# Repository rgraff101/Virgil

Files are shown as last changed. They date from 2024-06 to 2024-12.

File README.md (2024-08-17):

# BearCart

BearCart is an autonomous driving project. The goal is to upgrade an off-the-shelf
RC car into an AI powered self-driving platform. The software is running on a
Raspberry Pi 5 SBC in its native operating system: Raspberry Pi OS.
Visit [documentations](https://ucaengineeringphysics.github.io/BearCart/) for more details.
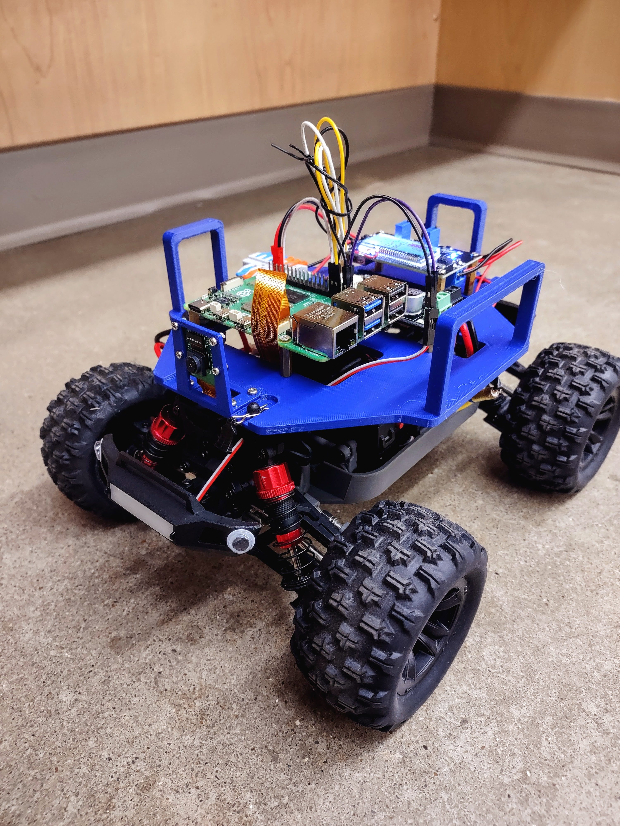
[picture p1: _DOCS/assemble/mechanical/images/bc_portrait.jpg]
portrait


This project is strongly inspired by the 
[DonkeyCar](https://github.com/autorope/donkeycar) project.

## Quick Start
Fire up the terminal on your Raspberry Pi, and run following commands in it.

### Install Dependencies 
```bash
sudo apt install python3-pip
pip install pip --upgrade --break-system-packages
```

### Clone The Repository
```bash
cd ~
git clone https://github.com/UCAEngineeringPhysics/BearCart.git
```

### Install Python Packages
```bash
cd ~/BearCart
pip install -r requirements.txt --break-system-packages
```

## Demo Videos
- [Initial BearCart](https://youtube.com/shorts/Kcm6qQqev3s)
- [Another Autopilot](https://youtu.be/8GX6HnfgrJQ)

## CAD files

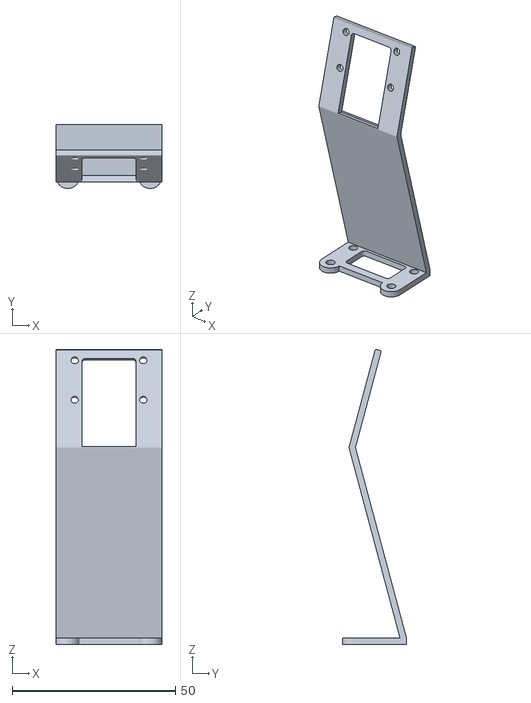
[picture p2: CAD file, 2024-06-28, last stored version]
_DOCS/mechanical_specs/3dprint/CameraMountTall.stl
32.4 x 19.6 x 90.3

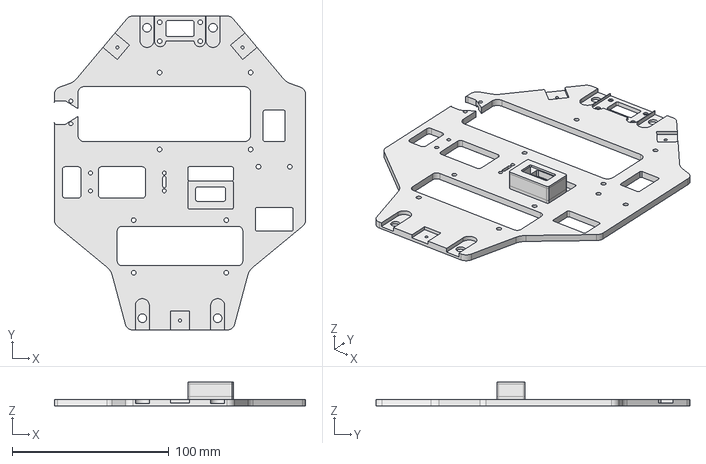
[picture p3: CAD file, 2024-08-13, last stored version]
mechanical_designs/mew4_bed_v3.FCStd
160.0 x 200.0 x 15.2 mm

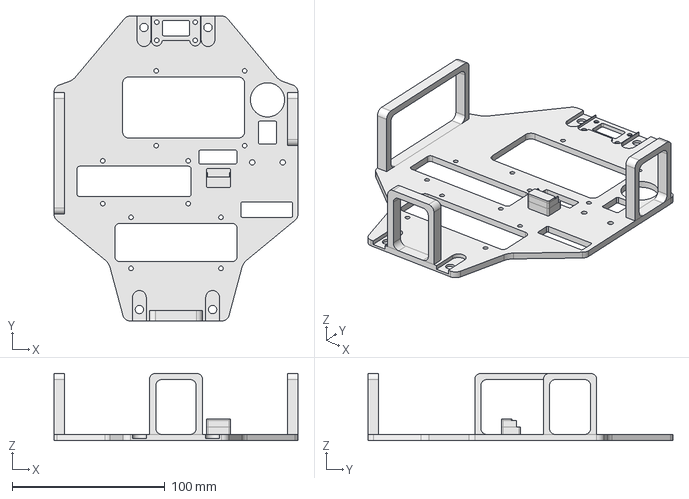
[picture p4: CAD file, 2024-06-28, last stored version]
_DOCS/mechanical_specs/3dprint/mew4_bed_v2.FCStd
160.0 x 200.0 x 44.0 mm

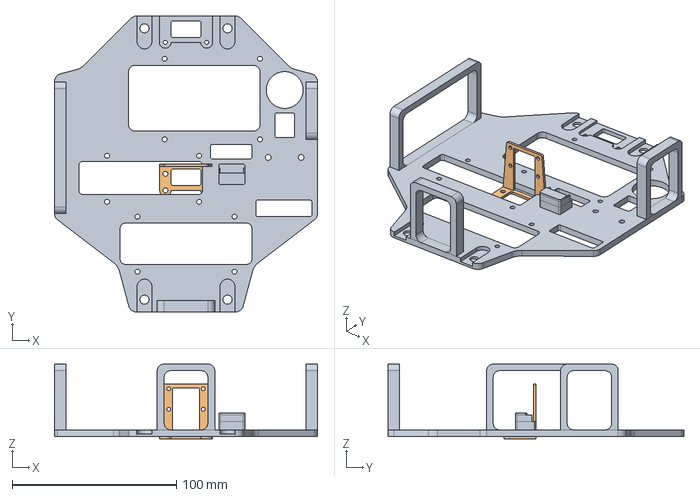
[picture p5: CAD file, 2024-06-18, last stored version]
_DOCS/mechanical_specs/3dprint/haiboxing_bed.FCStd
160.0 x 180.0 x 45.5 mm
CameraMount

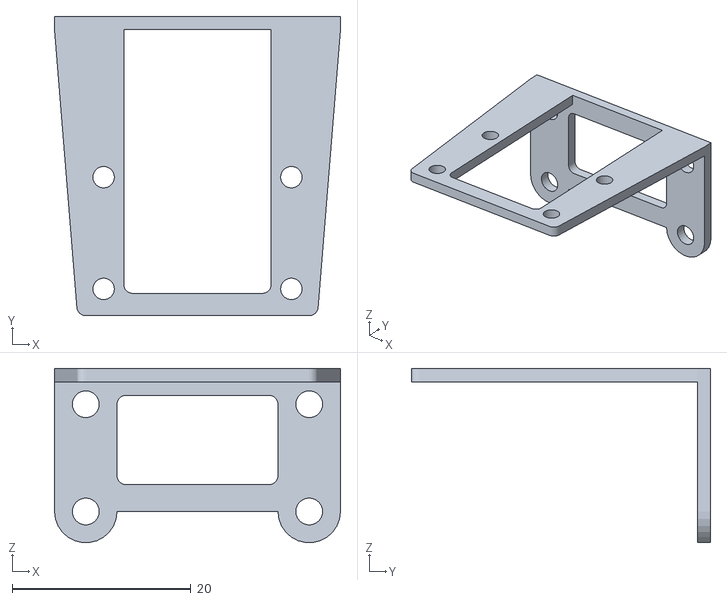
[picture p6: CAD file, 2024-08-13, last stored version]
mechanical_designs/CameraMount.stl
32.0 x 33.5 x 19.5

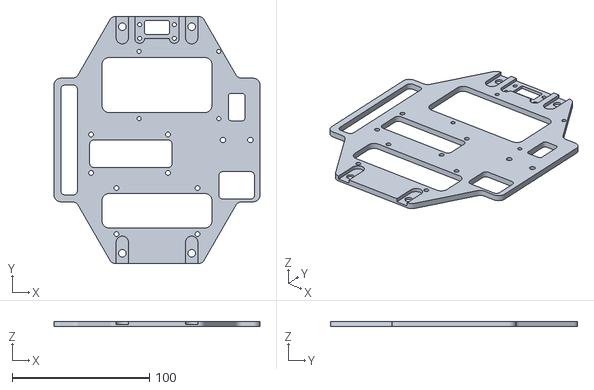
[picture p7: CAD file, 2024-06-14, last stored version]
_DOCS/mechanical_specs/3dprint/Foundation.stl
150.0 x 180.0 x 4.00

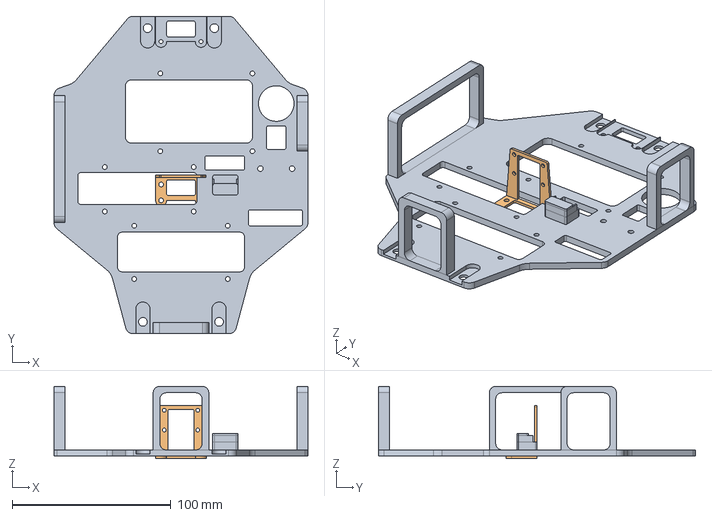
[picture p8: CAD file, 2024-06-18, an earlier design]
_DOCS/mechanical_specs/3dprint/mew4_bed.FCStd
160.0 x 200.0 x 45.5 mm
CameraMount

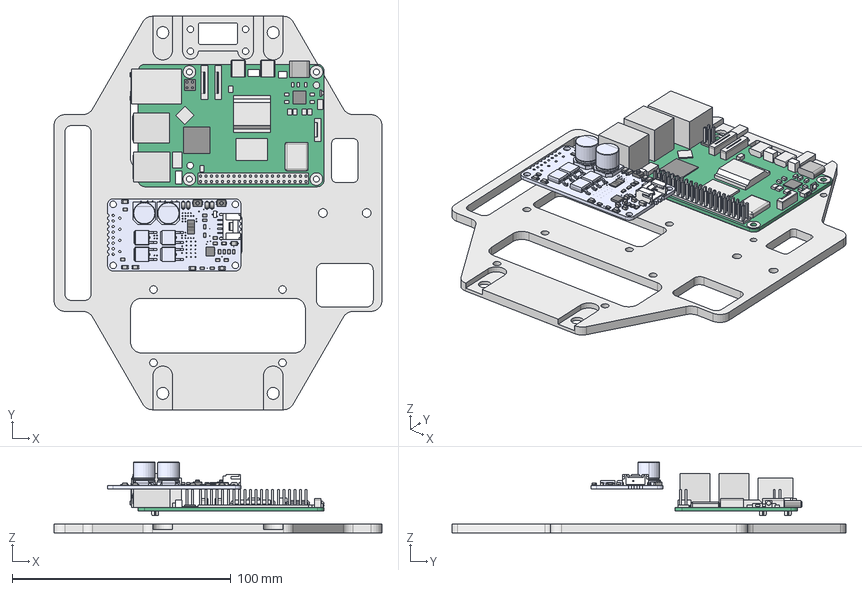
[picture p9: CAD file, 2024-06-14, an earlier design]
_DOCS/mechanical_specs/3dprint/electronics_foundation.FCStd
150.0 x 180.0 x 32.3 mm
MD13S PCB
C2012
C2013
C2014
C2015
C2016
R2012
R2013
R2014
R2015
R2016
R2017
R2018
R2019
R2020
R2021
R2022
R2023
D-SOD-123
D-SOD-124
D-SOD-125
D-SOD-126
D-SOD-127
LED-3216
LED-3217
LED-3218
LED-3219
LED-3220
GROVE-04-RA
SOT-23
DPAK
DPAK001
DPAK002
DPAK003
S-R-1W-6432
S-SP-2N-KAN0444
S-SP-2N-KAN0445
QFN24
SMD ECAP_10x10.7H
SMD ECAP_10x10.7H001
connector
CSI_DSI_connector
CSI_DSI_connector001
ethernet
gpio
hdmi-micro
hdmi-micro001
IR
mounting-holes
pcb
pcba-components Geometry
chips
pcie
pmic
poe Geometry
poe-pins
pwr-connector
rp1
switch
uart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

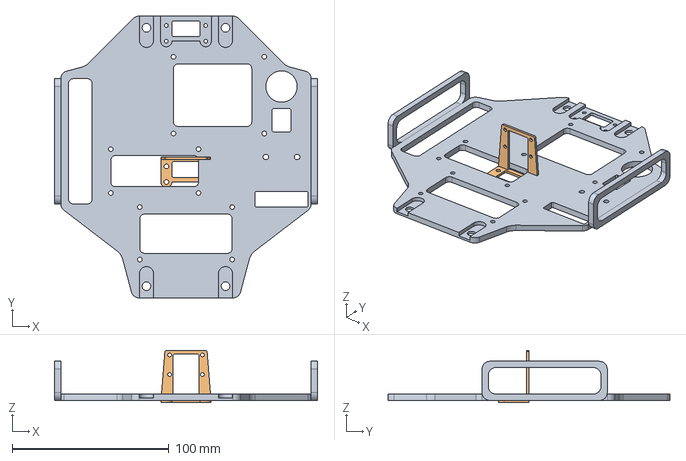
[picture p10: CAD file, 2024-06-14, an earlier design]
_DOCS/mechanical_specs/3dprint/electronics_foundation_v1.FCStd
168.0 x 180.0 x 33.5 mm
CameraMount

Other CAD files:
_DOCS/mechanical_specs/3dprint/electronics_foundation_v2.FCStd
_DOCS/mechanical_specs/3dprint/CameraMount.stl
mechanical_designs/mew4_bed_v2.FCStd
_DOCS/mechanical_specs/3dprint/electronics_foundation_v1.stl
_DOCS/mechanical_specs/3dprint/electronics_foundation_v2.stl
_DOCS/mechanical_specs/3dprint/haiboxing_bed.stl
_DOCS/mechanical_specs/3dprint/mew4_bed.stl
_DOCS/mechanical_specs/3dprint/mew4_bed_v2.stl
mechanical_designs/haiboxing_bed.stl
mechanical_designs/mew4_bed.stl
mechanical_designs/mew4_bed_v2.stl
mechanical_designs/mew4_bed_v3.stl

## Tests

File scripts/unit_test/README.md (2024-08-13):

# Unit Tests
Follow the order to test out BearCart's functionality unit by unit.

## 1. Blink Headlight
```console
python led.py
```

## 2. Find Buttons and Axes on Gamepad
```console
python joystick.py
```

## 3. Camera Preview
```console
python camera.py
```

## 4. Serial Communication
### 4.1 Transmit Throttle Dutycycle
```console
python serial_steering.py
```

### 4.2 Transmit Steering Dutycycle
```console
python serial_throttle.py
```

## 5. Control Steering and Throttle using Gamepad
```console
python joystick_drivetrain.py
```

## 6. Integrated Test with All Components
```console
python camera_joystick_drivetrain.py
```

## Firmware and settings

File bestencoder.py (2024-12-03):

import sys
from math import pi
from machine import Pin, PWM
from time import sleep

class Motor:

    def __init__(self, dir_pin, pwm_pin, enca_pin, encb_pin, slp_pin):
        # set pins
        self._dir_pin = Pin(dir_pin, Pin.OUT)
        self._pwm_pin = PWM(Pin(pwm_pin))
        self._enca_pin = Pin(enca_pin, Pin.IN, Pin.PULL_UP)
        self._encb_pin = Pin(encb_pin, Pin.IN, Pin.PULL_UP)
        self._slp_pin = Pin(slp_pin, Pin.OUT)  # Sleep pin
        self._pwm_pin.freq(1000)
        # stop motor
        self.disable()
        # interrupts
        self._enca_pin.irq(trigger=Pin.IRQ_RISING | Pin.IRQ_FALLING, handler=self._inc_counts)
        self._encb_pin.irq(trigger=Pin.IRQ_RISING | Pin.IRQ_FALLING, handler=self._inc_counts)
        # variables
        self.encoder_counts = 0

        # Stop motor initially
        self.stop()

    def _inc_counts(self, pin):
        self.encoder_counts += 1

    def stop(self):
        # Stop the motor and put to sleep
        self._pwm_pin.duty_u16(0)
        # self._slp_pin.value(0)  # Sleep motor

    def enable(self):
        self._slp_pin.value(1)

    def disable(self):
        self._pwm_pin.duty_ns(0)
        self._slp_pin.value(0)

    def forward(self, duty=1.0):
        # Move motor forward
        # self._slp_pin.value(1)  # Wake up motor
        self._dir_pin.value(0)
        self._pwm_pin.duty_u16(int(duty*65536))

    def backward(self, duty=1.0):
        # Move motor backward
        # self._slp_pin.value(1)  # Wake up motor
        self._dir_pin.value(1)
        self._pwm_pin.duty_u16(int(duty*65536))

    # def set_velocity(self, velocity):
    #     # For direct control, you can set desired velocity here
    #     self.target_velocity = velocity

    def reset_encoder(self):
        # Reset encoder counts
        self.encoder_counts = 0


if __name__ == "__main__":
    # Initialize your robot instance
    from machine import freq
    freq(200_000_000)
    # constants
    WHEEL_RADIUS = 0.0495  # m
    WHEEL_SEPARATION = 0.295  # m
    CPR = 64
    GEAR_RATIO = 70

    lm = Motor(3, 2, 14, 15, 4)
    rm = Motor(7, 6, 12, 13, 8)
    lm.enable()
    rm.enable()
    #  1 FORWARD 4.5 m
    target_distance = 5  # m
    target_counts = target_distance / (WHEEL_RADIUS * 2 * pi) * GEAR_RATIO * CPR
    print(f"target encoder counts: {target_counts}")
    while lm.encoder_counts < target_counts and rm.encoder_counts < target_counts:
        if lm.encoder_counts - rm.encoder_counts > 32:
            lm.stop()
            rm.forward(0.5)
        elif lm.encoder_counts - rm.encoder_counts < -32:
            lm.forward(0.5)
            rm.stop()
        else:
            lm.forward(0.5)
            rm.forward(0.5)
        sleep(0.01)
    lm.stop()
    rm.stop()
    sleep(1)
    lm.reset_encoder()
    rm.reset_encoder()
    # 1 TURN 90
    target_distance = WHEEL_SEPARATION / 2 * pi / 2.1  # m
    target_counts = target_distance / (WHEEL_RADIUS * 2 * pi) * GEAR_RATIO * CPR - 256
    print(f"target encoder counts: {target_counts}")
    while lm.encoder_counts < target_counts and rm.encoder_counts < target_counts:
        if lm.encoder_counts - rm.encoder_counts > 32:
            lm.stop()
            rm.forward(0.3)
        elif lm.encoder_counts - rm.encoder_counts < -32:
            lm.backward(0.3)
            rm.stop()
        else:
            lm.backward(0.3)
            rm.forward(0.3)
        sleep(0.01)
    lm.stop()
    rm.stop()
    sleep(1)
    lm.reset_encoder()
    rm.reset_encoder()
    # 2 FORWARD 8.5 m
    target_distance = 9  # m
    target_counts = target_distance / (WHEEL_RADIUS * 2 * pi) * GEAR_RATIO * CPR
    print(f"target encoder counts: {target_counts}")
    while lm.encoder_counts < target_counts and rm.encoder_counts < target_counts:
        if lm.encoder_counts - rm.encoder_counts > 32:
            lm.stop()
            rm.forward(0.5)
        elif lm.encoder_counts - rm.encoder_counts < -32:
            lm.forward(0.5)
            rm.stop()
        else:
            lm.forward(0.5)
            rm.forward(0.5)
        sleep(0.01)
    lm.stop()
    rm.stop()
    sleep(1)
    lm.reset_encoder()
    rm.reset_encoder()
    # 2 TURN 90
    target_distance = WHEEL_SEPARATION / 2 * pi / 2.3  # m
    target_counts = target_distance / (WHEEL_RADIUS * 2 * pi) * GEAR_RATIO * CPR - 256
    print(f"target encoder counts: {target_counts}")
    while lm.encoder_counts < target_counts and rm.encoder_counts < target_counts:
        if lm.encoder_counts - rm.encoder_counts > 32:
            lm.stop()
            rm.forward(0.3)
        elif lm.encoder_counts - rm.encoder_counts < -32:
            lm.backward(0.3)
            rm.stop()
        else:
            lm.backward(0.3)
            rm.forward(0.3)
        sleep(0.01)
    lm.stop()
    rm.stop()
    sleep(1)
    lm.reset_encoder()
    rm.reset_encoder()
    # 3 FORWARD 4.5 m
    target_distance = 3.3  # m
    target_counts = target_distance / (WHEEL_RADIUS * 2 * pi) * GEAR_RATIO * CPR
    print(f"target encoder counts: {target_counts}")
    while lm.encoder_counts < target_counts and rm.encoder_counts < target_counts:
        if lm.encoder_counts - rm.encoder_counts > 32:
            lm.stop()
            rm.forward(0.5)
        elif lm.encoder_counts - rm.encoder_counts < -32:
            lm.forward(0.5)
            rm.stop()
        else:
            lm.forward(0.5)
            rm.forward(0.5)
        sleep(0.01)
    lm.stop()
    rm.stop()
    sleep(1)
    lm.reset_encoder()
    rm.reset_encoder()
    # 3 TURN 90
    target_distance = WHEEL_SEPARATION / 2 * pi / 2.1  # m
    target_counts = target_distance / (WHEEL_RADIUS * 2 * pi) * GEAR_RATIO * CPR - 256
    print(f"target encoder counts: {target_counts}")
    while lm.encoder_counts < target_counts and rm.encoder_counts < target_counts:
        if lm.encoder_counts - rm.encoder_counts > 32:
            lm.stop()
            rm.forward(0.3)
        elif lm.encoder_counts - rm.encoder_counts < -32:
            lm.backward(0.3)
            rm.stop()
        else:
            lm.backward(0.3)
            rm.forward(0.3)
        sleep(0.01)
    lm.stop()
    rm.stop()
    sleep(1)
    lm.reset_encoder()
    rm.reset_encoder()
    # 4 FORWARD 4.5 m
    target_distance = 6.8  # m
    target_counts = target_distance / (WHEEL_RADIUS * 2 * pi) * GEAR_RATIO * CPR
    print(f"target encoder counts: {target_counts}")
    while lm.encoder_counts < target_counts and rm.encoder_counts < target_counts:
        if lm.encoder_counts - rm.encoder_counts > 32:
            lm.stop()
            rm.forward(0.5)
        elif lm.encoder_counts - rm.encoder_counts < -32:
            lm.forward(0.5)
            rm.stop()
        else:
            lm.forward(0.5)
            rm.forward(0.5)
        sleep(0.01)
    lm.stop()
    rm.stop()
    sleep(1)
    lm.reset_encoder()
    rm.reset_encoder()
    # 4 TURN 90
    target_distance = WHEEL_SEPARATION / 2 * pi / 1.8  # m
    target_counts = target_distance / (WHEEL_RADIUS * 2 * pi) * GEAR_RATIO * CPR - 256
    print(f"target encoder counts: {target_counts}")
    while lm.encoder_counts < target_counts and rm.encoder_counts < target_counts:
        if lm.encoder_counts - rm.encoder_counts > 32:
            lm.stop()
            rm.backward(0.3)
        elif lm.encoder_counts - rm.encoder_counts < -32:
            lm.forward(0.3)
            rm.stop()
        else:
            lm.forward(0.3)
            rm.backward(0.3)
        sleep(0.01)
    lm.stop()
    rm.stop()
    sleep(1)
    lm.reset_encoder()
    rm.reset_encoder()
    
    # 5 FORWARD 4.5 m
    target_distance = 2.3  # m
    target_counts = target_distance / (WHEEL_RADIUS * 2 * pi) * GEAR_RATIO * CPR
    print(f"target encoder counts: {target_counts}")
    while lm.encoder_counts < target_counts and rm.encoder_counts < target_counts:
        if lm.encoder_counts - rm.encoder_counts > 32:
            lm.stop()
            rm.forward(0.5)
        elif lm.encoder_counts - rm.encoder_counts < -32:
            lm.forward(0.5)
            rm.stop()
        else:
            lm.forward(0.5)
            rm.forward(0.5)
        sleep(0.01)
    lm.stop()
    rm.stop()
    sleep(1)
    lm.reset_encoder()
    rm.reset_encoder()
    # 5  TURN 90
    target_distance = WHEEL_SEPARATION / 2 * pi / 1.9  # m
    target_counts = target_distance / (WHEEL_RADIUS * 2 * pi) * GEAR_RATIO * CPR - 256
    print(f"target encoder counts: {target_counts}")
    while lm.encoder_counts < target_counts and rm.encoder_counts < target_counts:
        if lm.encoder_counts - rm.encoder_counts > 32:
            lm.stop()
            rm.backward(0.3)
        elif lm.encoder_counts - rm.encoder_counts < -32:
            lm.forward(0.3)
            rm.stop()
        else:
            lm.forward(0.3)
            rm.backward(0.3)
        sleep(0.01)
    lm.stop()
    rm.stop()
    sleep(1)
    lm.reset_encoder()
    rm.reset_encoder()
    
    #     # FORWARD 4.5 m
    target_distance = 7.3  # m
    target_counts = target_distance / (WHEEL_RADIUS * 2 * pi) * GEAR_RATIO * CPR
    print(f"target encoder counts: {target_counts}")
    while lm.encoder_counts < target_counts and rm.encoder_counts < target_counts:
        if lm.encoder_counts - rm.encoder_counts > 32:
            lm.stop()
            rm.forward(0.5)
        elif lm.encoder_counts - rm.encoder_counts < -32:
            lm.forward(0.5)
            rm.stop()
        else:
            lm.forward(0.5)
            rm.forward(0.5)
        sleep(0.01)
    lm.stop()
    rm.stop()
    sleep(1)
    lm.reset_encoder()
    rm.reset_encoder()
    # TURN 90
    target_distance = WHEEL_SEPARATION / 2 * pi / 1.9  # m
    target_counts = target_distance / (WHEEL_RADIUS * 2 * pi) * GEAR_RATIO * CPR - 256
    print(f"target encoder counts: {target_counts}")
    while lm.encoder_counts < target_counts and rm.encoder_counts < target_counts:
        if lm.encoder_counts - rm.encoder_counts > 32:
            lm.stop()
            rm.forward(0.3)
        elif lm.encoder_counts - rm.encoder_counts < -32:
            lm.backward(0.3)
            rm.stop()
        else:
            lm.backward(0.3)
            rm.forward(0.3)
        sleep(0.01)
    lm.stop()
    rm.stop()
    sleep(1)
    lm.reset_encoder()
    rm.reset_encoder()
    # 3 FORWARD 4.5 m
    target_distance = 3.75  # m
    target_counts = target_distance / (WHEEL_RADIUS * 2 * pi) * GEAR_RATIO * CPR
    print(f"target encoder counts: {target_counts}")
    while lm.encoder_counts < target_counts and rm.encoder_counts < target_counts:
        if lm.encoder_counts - rm.encoder_counts > 32:
            lm.stop()
            rm.forward(0.5)
        elif lm.encoder_counts - rm.encoder_counts < -32:
            lm.forward(0.5)
            rm.stop()
        else:
            lm.forward(0.5)
            rm.forward(0.5)
        sleep(0.01)
    lm.stop()
    rm.stop()
    sleep(1)
    lm.reset_encoder()
    rm.reset_encoder()
    # 3 TURN 90
    target_distance = WHEEL_SEPARATION / 2 * pi / 2.2  # m
    target_counts = target_distance / (WHEEL_RADIUS * 2 * pi) * GEAR_RATIO * CPR - 256
    print(f"target encoder counts: {target_counts}")
    while lm.encoder_counts < target_counts and rm.encoder_counts < target_counts:
        if lm.encoder_counts - rm.encoder_counts > 32:
            lm.stop()
            rm.forward(0.3)
        elif lm.encoder_counts - rm.encoder_counts < -32:
            lm.backward(0.3)
            rm.stop()
        else:
            lm.backward(0.3)
            rm.forward(0.3)
        sleep(0.01)
    lm.stop()
    rm.stop()
    sleep(1)
    lm.reset_encoder()
    rm.reset_encoder()

    # 9 FORWARD 4.5 m
    target_distance = 9  # m
    target_counts = target_distance / (WHEEL_RADIUS * 2 * pi) * GEAR_RATIO * CPR
    print(f"target encoder counts: {target_counts}")
    while lm.encoder_counts < target_counts and rm.encoder_counts < target_counts:
        if lm.encoder_counts - rm.encoder_counts > 32:
            lm.stop()
            rm.forward(0.5)
        elif lm.encoder_counts - rm.encoder_counts < -32:
            lm.forward(0.5)
            rm.stop()
        else:
            lm.forward(0.5)
            rm.forward(0.5)
        sleep(0.01)
    lm.stop()
    rm.stop()
    sleep(1)
    lm.reset_encoder()
    rm.reset_encoder()
    
    # 3 TURN 90
    target_distance = WHEEL_SEPARATION / 2 * pi / 2.2  # m
    target_counts = target_distance / (WHEEL_RADIUS * 2 * pi) * GEAR_RATIO * CPR - 256
    print(f"target encoder counts: {target_counts}")
    while lm.encoder_counts < target_counts and rm.encoder_counts < target_counts:
        if lm.encoder_counts - rm.encoder_counts > 32:
            lm.stop()
            rm.forward(0.3)
        elif lm.encoder_counts - rm.encoder_counts < -32:
            lm.backward(0.3)
            rm.stop()
        else:
            lm.backward(0.3)
            rm.forward(0.3)
        sleep(0.01)
    lm.stop()
    rm.stop()
    sleep(1)
    lm.reset_encoder()
    rm.reset_encoder()
    
    # 9 FORWARD 4.5 m
    target_distance = 7  # m
    target_counts = target_distance / (WHEEL_RADIUS * 2 * pi) * GEAR_RATIO * CPR
    print(f"target encoder counts: {target_counts}")
    while lm.encoder_counts < target_counts and rm.encoder_counts < target_counts:
        if lm.encoder_counts - rm.encoder_counts > 32:
            lm.stop()
            rm.forward(0.5)
        elif lm.encoder_counts - rm.encoder_counts < -32:
            lm.forward(0.5)
            rm.stop()
        else:
            lm.forward(0.5)
            rm.forward(0.5)
        sleep(0.01)
    lm.stop()
    rm.stop()
    sleep(1)
    lm.reset_encoder()
    rm.reset_encoder()
    
    lm.disable()
    rm.disable()
    freq(125_000_000)

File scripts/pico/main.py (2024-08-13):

"""
Upload this script to the pico board, then rename it to main.py.
Read dutycycle in nanoseconds via USB BUS.
"""
import sys
import select
from time import sleep
from machine import Pin, PWM

# SETUP
steering = PWM(Pin(0))
steering.freq(50)
throttle = PWM(Pin(15))
throttle.freq(50)
sleep(3)  # ESC calibrate
poller = select.poll()
poller.register(sys.stdin, select.POLLIN)
event = poller.poll()

# LOOP
while True:
    # read data from serial
    for msg, _ in event:
        buffer = msg.readline().rstrip().split(',')
        if len(buffer) == 2:
            ns_st, ns_th = int(buffer[0]), int(buffer[1])
            steering.duty_ns(ns_st)
            throttle.duty_ns(ns_th)

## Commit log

2024-05-29 import freecad project
    [rc_base.FCStd]
2024-05-29 init new design
    [electronics_foundation.FCStd]
2024-05-29 create base
    [electronics_foundation.FCStd]
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2024-05-29 set rpi mounting
    [electronics_foundation.FCStd]
2024-05-29 import MD13S model
    [electronics_foundation.FCStd]
2024-05-29 import rpi5 model
    [electronics_foundation.FCStd]
2024-05-29 relocate rpi mount
    [electronics_foundation.FCStd]
2024-05-29 place MD13S mount
    [electronics_foundation.FCStd]
2024-05-30 place wire spliter
    [electronics_foundation.FCStd]
2024-05-30 more mounting holes
    [electronics_foundation.FCStd]
2024-05-30 place cam holder
    [electronics_foundation.FCStd]
2024-05-30 place cam mount
    [electronics_foundation.FCStd]
2024-05-30 mod camera mount
    [electronics_foundation.FCStd]
2024-05-30 export stl
    [CameraMount.stl, Foundation.stl, electronics_foundation.FCStd]
2024-05-30 place pin pockets
    [electronics_foundation.FCStd]
2024-05-30 export foundation stl
    [Foundation.stl]
2024-05-31 create base_link
    [electronics_foundation_v1.FCStd]
2024-05-31 add mounting holes to base_link
    [electronics_foundation_v1.FCStd]
2024-05-31 add rpi mounting holes to base_link
    [electronics_foundation_v1.FCStd]
2024-05-31 add md13s mounting holes
    [electronics_foundation_v1.FCStd]
2024-05-31 add pin slots and more mounting holes
    [electronics_foundation_v1.FCStd]
2024-05-31 add wire and switch holes
    [electronics_foundation_v1.FCStd]
2024-05-31 add ventilation holes
    [electronics_foundation_v1.FCStd]
2024-05-31 add right handle
    [electronics_foundation_v1.FCStd]
2024-05-31 add left handle
    [electronics_foundation_v1.FCStd]
2024-05-31 save changes
    [electronics_foundation_v1.FCStd]
2024-05-31 test camera using picam2
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2024-06-09 copy v1 to init v2
    [electronics_foundation_v2.FCStd]
2024-06-09 update design
    [electronics_foundation_v2.FCStd]
2024-06-10 update design with handle pads
    [electronics_foundation_v2.FCStd]
2024-06-10 update design to v2
    [electronics_foundation_v2.FCStd, electronics_foundation_v2.stl]
2024-06-11 update v2
    [electronics_foundation_v2.FCStd, electronics_foundation_v2.stl]
2024-06-11 update v2 with new 5v regulator stand
    [electronics_foundation_v2.FCStd, electronics_foundation_v2.stl]
2024-06-12 add stand walls to v2 design
    [electronics_foundation_v2.FCStd, electronics_foundation_v2.stl]
2024-06-13 add a cap for regulator stand
    [electronics_foundation_v2.FCStd, electronics_foundation_v2.stl]
2024-06-13 extend 5v regulator stand lid
    [electronics_foundation_v2.FCStd, electronics_foundation_v2.stl]
2024-06-14 rename regulators sketches
    [electronics_foundation_v2.FCStd]
2024-06-14 fix no planar face issue
    [electronics_foundation_v2.FCStd, electronics_foundation_v2.stl]
2024-06-14 update motor driver pin
2024-06-14 use 'q' to exit camera test
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2024-06-14 update camera test format, ignore alpha channel
2024-06-14 fix image retrieve from dataset
    [train.py]
2024-06-14 update autopilot but having segmentation fault error
    [autopilot.py]
2024-06-15 enlarge switch hole
    [electronics_foundation_v2.FCStd, electronics_foundation_v2.stl]
2024-06-15 remove old designs
    [Foundation.stl, electronics_foundation.FCStd, electronics_foundation_v1.FCStd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]
2024-06-15 create bed for mew4 car
    [mew4_bed.FCStd, mew4_bed.stl]
2024-06-15 fix mew4 bed, add nut holders
    [mew4_bed.FCStd, mew4_bed.stl]
2024-06-16 adjust support mounting
    [mew4_bed.FCStd, mew4_bed.stl]
2024-06-16 rename haiboxing bed files
    [haiboxing_bed.FCStd, haiboxing_bed.stl]
2024-06-16 adjust cam holder slot depth
    [haiboxing_bed.FCStd, haiboxing_bed.stl, mew4_bed.FCStd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]
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2024-06-19 fix servo test
2024-06-19 rename throttle and steer test scripts
2024-06-19 add led to integrated test
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2024-06-28 create mew4 bed v2
    [CameraMountTall.stl, mew4_bed_v2.FCStd, mew4_bed_v2.stl]
2024-06-28 update mew4 v2 design
    [CameraMountTall.stl, mew4_bed_v2.FCStd, mew4_bed_v2.stl]
2024-06-29 add wire splitter diagram
2024-06-29 add power diagram for pi
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2024-06-30 update standoffs installation instructions
2024-06-30 update standoff installation illustrations and instructions
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2024-07-01 add servo power line instructions
2024-07-01 update servo wiring diagram
2024-07-01 add motor driver wiring
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2024-07-02 add integrated wiring diagram
2024-07-08 update camera mount design
    [CameraMount.stl, mew4_bed_v2.FCStd]
2024-07-10 add led test code
2024-07-21 update esc motor driver
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2024-07-24 calibrate esc motor control
2024-07-24 add 3 sec pause after instantiate engine to set throttle range
2024-07-25 add throttle communication tests
2024-07-25 add joystick controlled throttle test
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2024-07-29 update joystick control servo test
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2024-07-30 reorganize mechanical design
    [CameraMount.stl, CameraMountTall.stl, haiboxing_bed.FCStd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]
2024-07-30 start new design
    [mew4_bed_v3.FCStd]
2024-07-31 update pico on bed
    [mew4_bed_v3.FCStd]
2024-07-31 update v3 design
    [mew4_bed_v3.FCStd]
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2024-08-12 update joystick drivetrain control test
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2024-08-12 minor fix joystick drivetrain test
    [joystick_drivetrain.py, main.py]
2024-08-12 fix serial port name
    [joystick_drivetrain.py]
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2024-08-13 add new integrated test
    camera, joystick, drivetrain tested together
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2024-08-13 update integrated test
    camera, led, throttle, steering, gamepad all tested
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2024-11-07 remove non-software
    [CameraMount.stl, CameraMountTall.stl, haiboxing_bed.FCStd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]
